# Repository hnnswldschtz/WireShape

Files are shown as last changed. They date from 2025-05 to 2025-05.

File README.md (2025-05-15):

# WireShape

*WireShape CNC* is a cnc-wirebending machine and CAM control software. Our low-cost machine design is similar to commercially available wire benders (such as the DI Wire), but constructed from widely available 3D-printer components, 3D-printed mechanics, stepper motors, open source control electronics, and a CNC-milled wooden base frame. 

For more details and background, check this source:
https://dl.acm.org/doi/10.1145/3623263.3623363

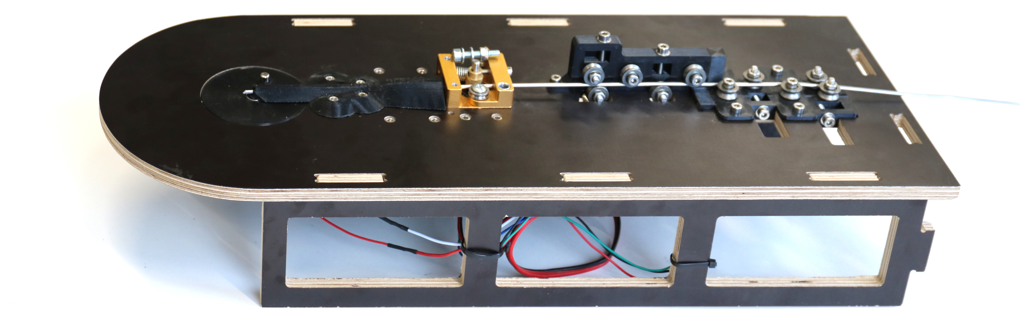
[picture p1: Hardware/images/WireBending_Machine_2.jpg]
machine


## WireShape_CAM_Processor
svg to gcode parser and interpreter for the  
Wireshape process (freiform-heißpress). 
previews shape, outputs gcode file for the CNC Wireshaper. 

dependencies: 
- matplolib 
- svg.path

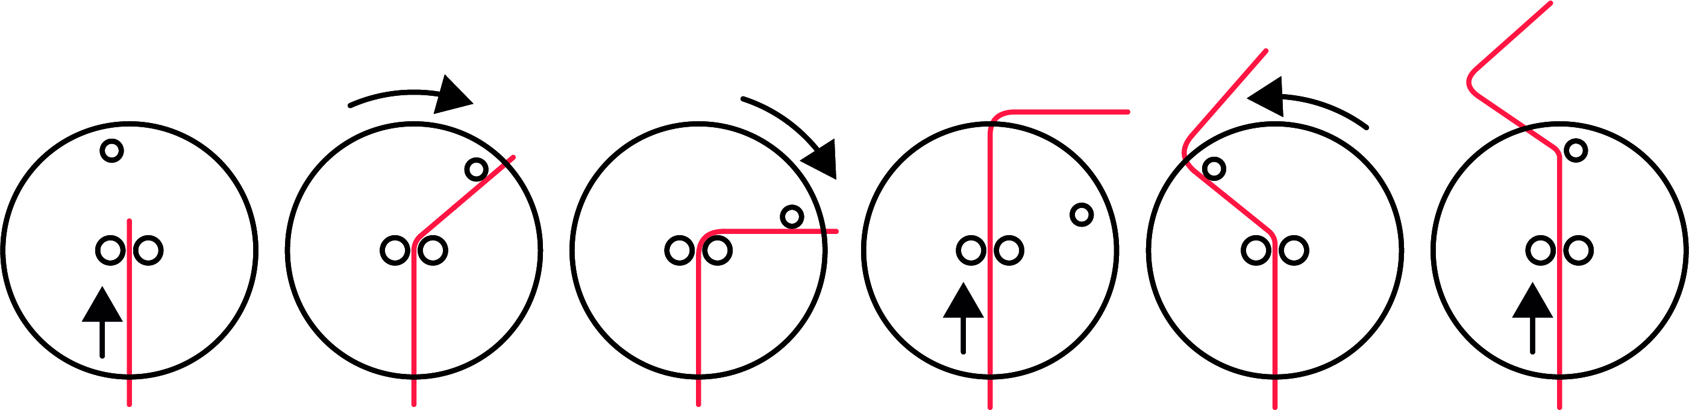
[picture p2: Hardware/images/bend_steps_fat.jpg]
bedning steps

Principle of the CNC wire bending mechanism

## Wire Shape Hardware

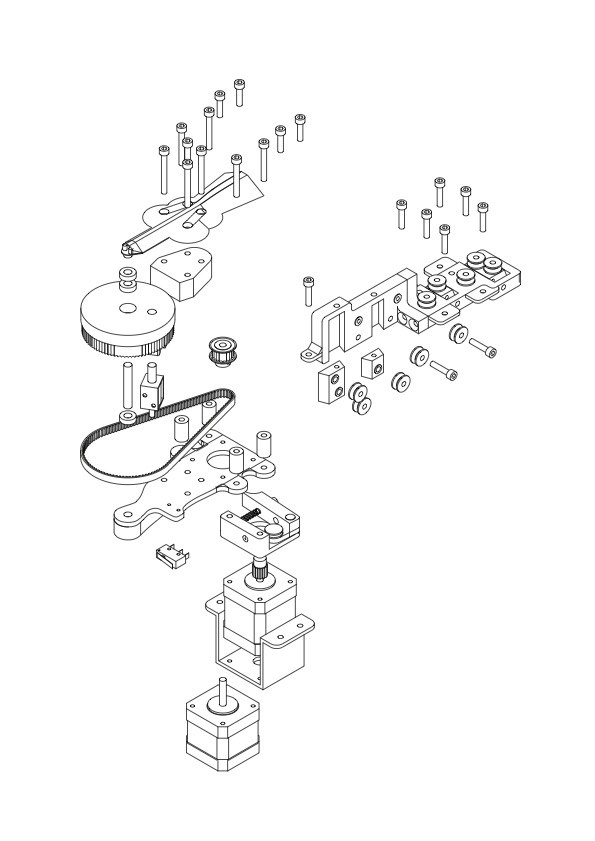
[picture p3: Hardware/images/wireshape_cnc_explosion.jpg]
assembly


### Wireshape CNC BOM

#### Electronics
+ 1x Arduino Uno R3
+ 1x Arduino CNC shield eg https://www.ebay.de/itm/253692368532
+ 3x DRV8825 stepper driver
+ 2 x stepper motor nema 17 
+ 1x Feeder:  https://www.amazon.de/Dasing-Extruder-Bausatz-Aluminium-Creality-Rot/dp/B087F75JXY

+ 1 solenoid ncd03212v - https://linhkiendientu.vn/san-pham/chot-nam-cham-dien-day-keo-0.5n-12v-ncd03212v
+ FET driver for solenoid, like: https://www.amazon.de/Treibermodul-Dual-Hochleistungs-Switching-Schalttafel-Ar-duino/dp/B0DG8B58PM
+ Powersupply 12V

#### Mechanics
+ 1x Belt - Polyurethane timing belt T2.5 width 6mm Lw 330 132 teeth - https://www.maedler.de/Article/16061200

+ 1x Pulley - Timing belt pulley T2.5 material aluminium 20 teeth for belt width 10mm https://www.maedler.de/Article/16032000
+ 1x Axis (cut to 37 mm) -  Silver steel DIN 175 115CrV3 ground and polished diameter 6h9 x 500mm long https://www.maedler.de/Article/64700600
+ 3x Bearing for axis:  6x12x4 mmMR-126-2RS https://www.kugellager-express.de/high-precision-miniature-ball-bearing-hc-mr126-2rs-cn-p6-gs1-6x12x4-mm
+ Chassis - 9mm plywood
+ 10 x V-Groove ball bearing 4x13x6mm (ID,OD,Thk) (for straightener)
eg https://ebay.us/m/v5IUZD

#### Screws
Socket head cap screw (hex):
+ 4x  M4x16
+ 13x M4x20
+ 4x  M4x30
+ 4x  M4x35
+ 4 x M3x12 (stepper mount)

Countersunk head screw (straightener):
+ 6x M4x20

Nuts
+ 10 x M4 nut
+ 20 x M4 Nut, self locking

The Filament straightener section is based on Jonatan Bloms Work reelased under CC BY 4.0:
https://www.thingiverse.com/thing:1552283

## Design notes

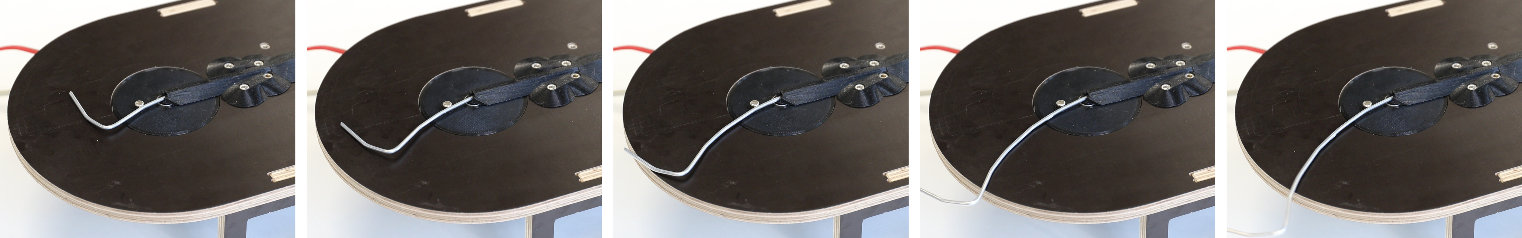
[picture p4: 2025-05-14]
Hardware/images/wirebending_curve.jpg

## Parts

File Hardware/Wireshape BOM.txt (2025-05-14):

WIRESHAPE CNC BOM
-------------------------------

1x Arduino Uno R3
1x Arduino CNC shield eg https://www.ebay.de/itm/253692368532
3x DRV8825 stepper driver
2 x stepper motor nema 17 
1x Feeder:  https://www.amazon.de/Dasing-Extruder-Bausatz-Aluminium-Creality-Rot/dp/B087F75JXY

1 solenoid ncd03212v - https://linhkiendientu.vn/san-pham/chot-nam-cham-dien-day-keo-0.5n-12v-ncd03212v
FET driver for solenoid like: https://www.amazon.de/Treibermodul-Dual-Hochleistungs-Switching-Schalttafel-Ar-duino/dp/B0DG8B58PM
Powersupply 12V

1x Belt - Polyurethane timing belt T2.5 width 6mm Lw 330 132 teeth - https://www.maedler.de/Article/16061200
1x Pulley - Timing belt pulley T2.5 material aluminium 20 teeth for belt width 10mm https://www.maedler.de/Article/16032000
1x Axis (cut to 37 mm) -  Silver steel DIN 175 115CrV3 ground and polished diameter 6h9 x 500mm long https://www.maedler.de/Article/64700600

3x Bearing for axis:  6x12x4 mmMR-126-2RS https://www.kugellager-express.de/high-precision-miniature-ball-bearing-hc-mr126-2rs-cn-p6-gs1-6x12x4-mm

Chassis - 9mm plywood

10 x V-Groove ball bearing 4x13x6mm (ID,OD,Thk) (for straightener)
http://www.ebay.com/itm/10Pcs-Metal-Sealed-Guide-Wire-Line-Track-Deep-V-Groove-Pulley-Rail-Ball-Bearing-/321898243903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

###########screws########

10 x M4 nut
20 x M4 Nut, self locking

Socket head cap screw (hex):
4x  M4x16
13x M4x20
4x  M4x30
4x  M4x35
4 x M3x12 (stepper mount)

Countersunk head screw (straightener):
6x M4x20

Details about Filament straightener 
https://www.thingiverse.com/thing:1552283

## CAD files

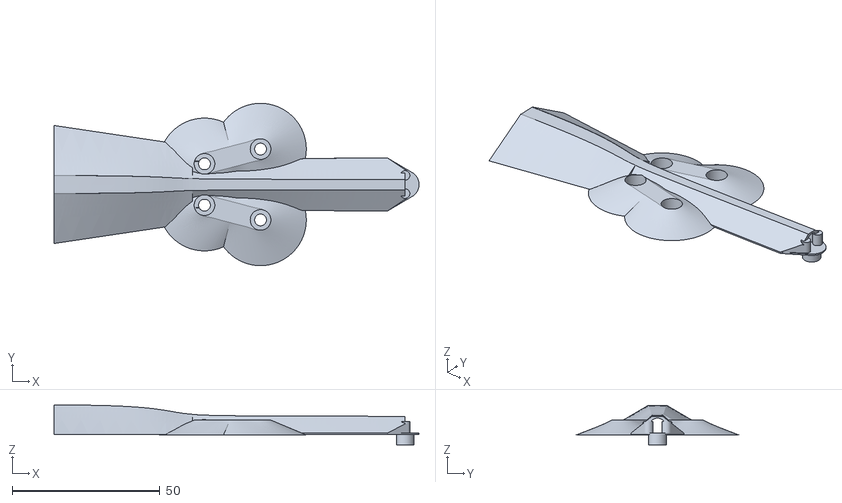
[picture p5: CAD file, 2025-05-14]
Hardware/3D print files/Machine 3d Print Parts/wireshape_cnc_wire_guide.stl
123.7 x 55.0 x 13.5

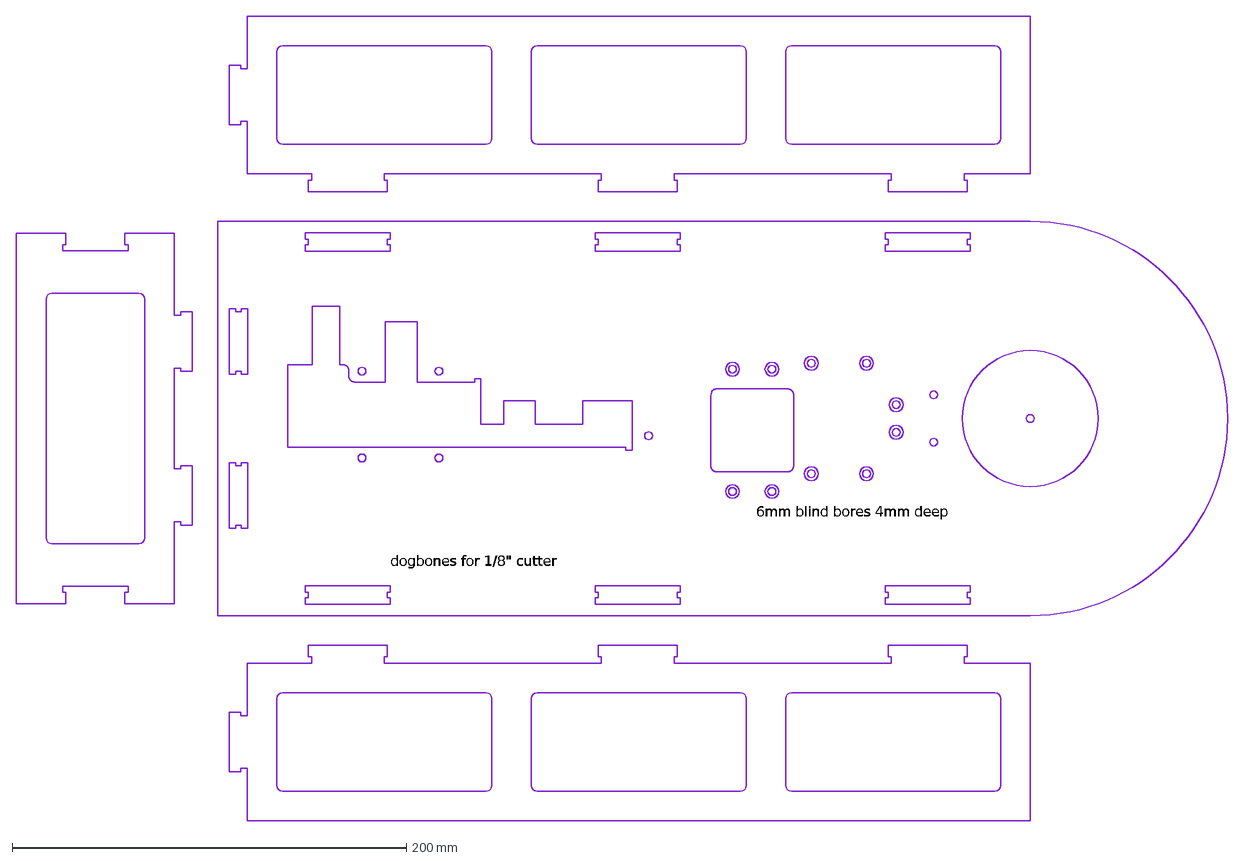
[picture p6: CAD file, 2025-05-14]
Hardware/milling/wireshape_cnc_wood_milling_drilling_9mm.dxf
dogbones for 1/8" cutter
6mm blind bores 4mm deep

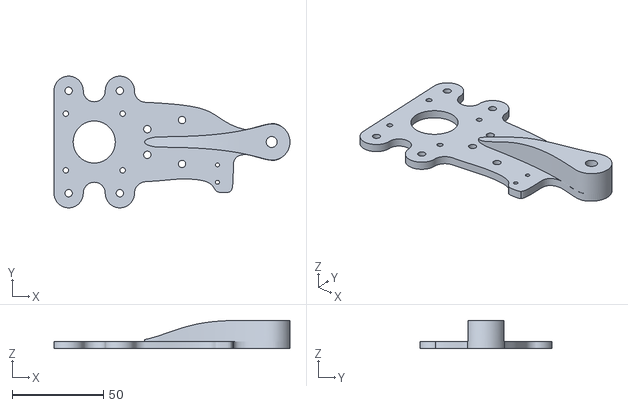
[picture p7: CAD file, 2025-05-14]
Hardware/3D print files/Machine 3d Print Parts/wireshape_cnc_belt_gear_structure.stl
129.0 x 72.0 x 15.5

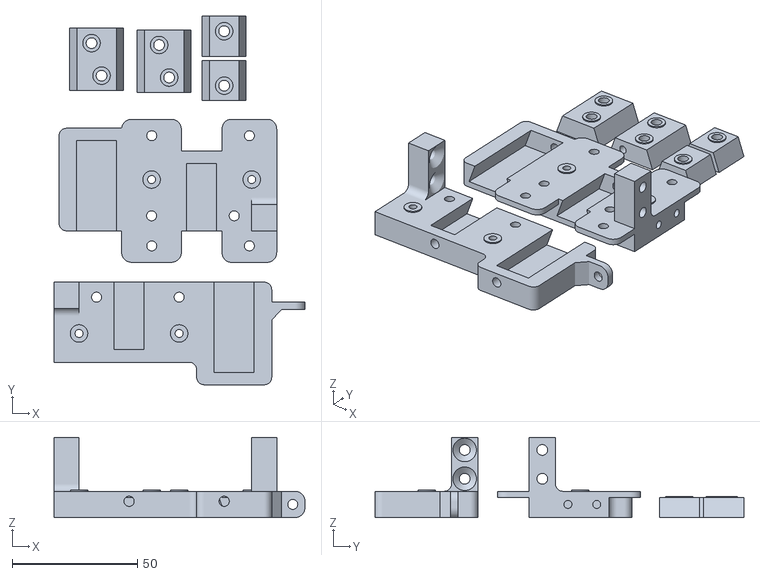
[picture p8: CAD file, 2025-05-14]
Hardware/3D print files/Machine 3d Print Parts/wireshape_cnc_wire_straightener.stl
100.3 x 147.2 x 32.0

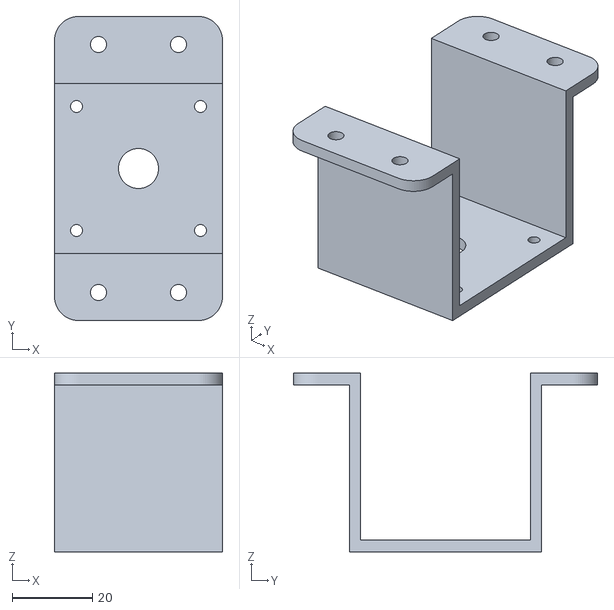
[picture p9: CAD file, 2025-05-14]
Hardware/3D print files/Machine 3d Print Parts/wireshape_cnc_motor_holder.stl
42.0 x 76.0 x 44.7

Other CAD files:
Hardware/3D print files/Manual Jig/Wire_Jig_KRX_with_valve_modified.3dm

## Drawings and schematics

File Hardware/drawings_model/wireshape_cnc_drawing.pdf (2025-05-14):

512.0

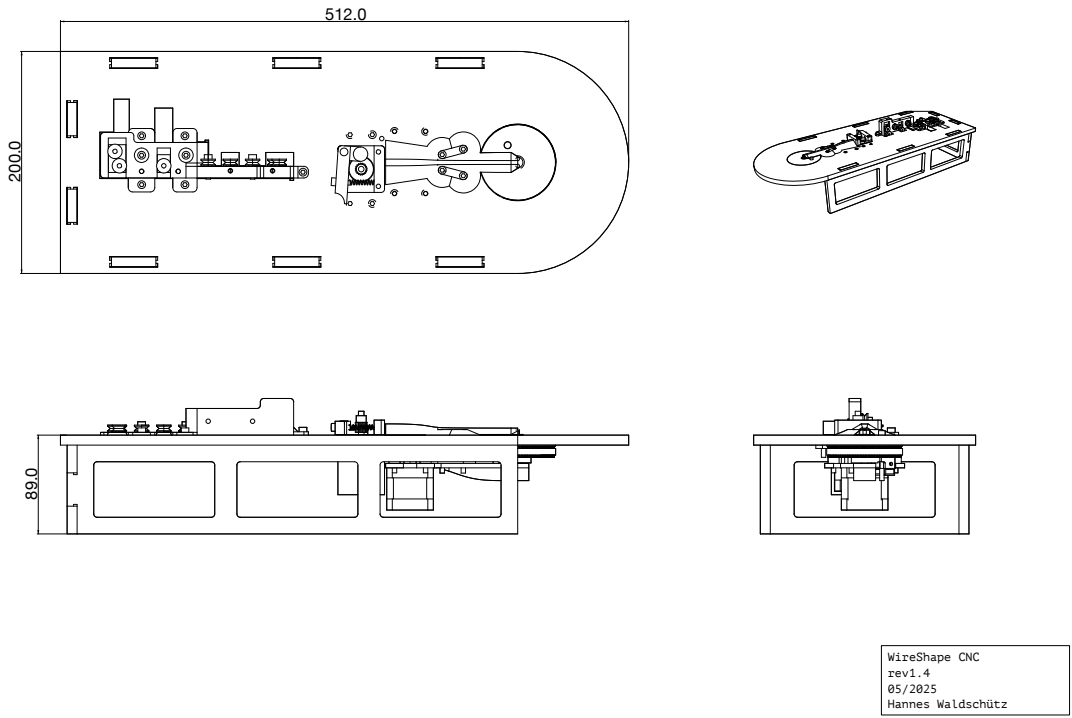
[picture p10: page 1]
WireShape CNC rev1.4 05/2025 Hannes Waldschütz

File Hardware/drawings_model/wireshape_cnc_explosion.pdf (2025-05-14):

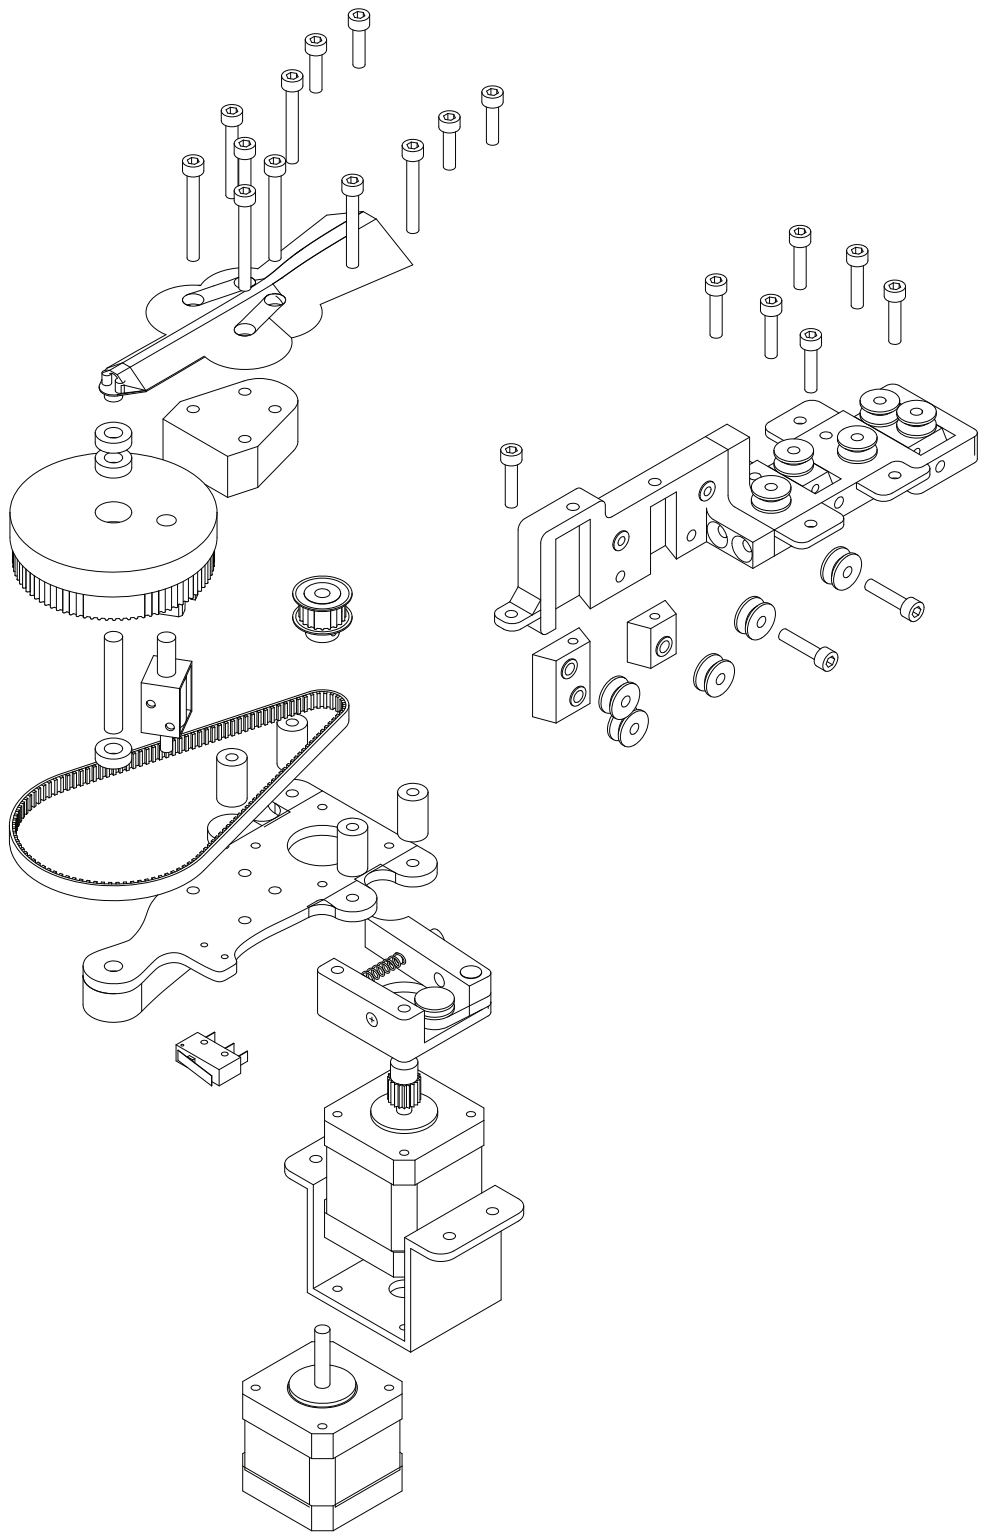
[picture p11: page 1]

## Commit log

2025-05-14 Create Wireshape BOM.txt
2025-05-14 update landing
